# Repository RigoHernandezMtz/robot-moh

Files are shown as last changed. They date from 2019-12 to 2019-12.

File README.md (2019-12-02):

# Robot Moh

## Robot móvil para navegación

Este repositorio contiene los archivos necesarios para poner a funcionar el robot, como:

- Diagrama y PCB en documentos de Eagle
- Archivos de CAD del chasis en formato de Siemens Unigraphics NX 10.5
- Lista de materiales en documento de Excel, y de corte laser del chasis en PDF.
- Codigos, del arduino y de la Raspberry Pi o BeagleBone Black

### Diseño en CAD del robot
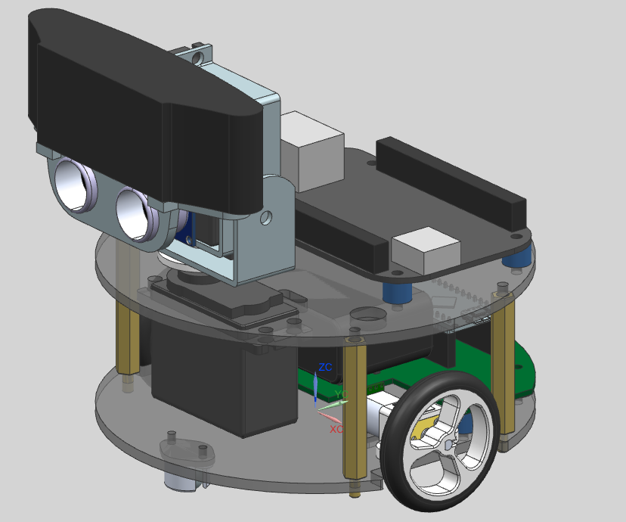
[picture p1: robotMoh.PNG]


---

Diseñado por: **Ing. Gerardo Ramos Vasquez**

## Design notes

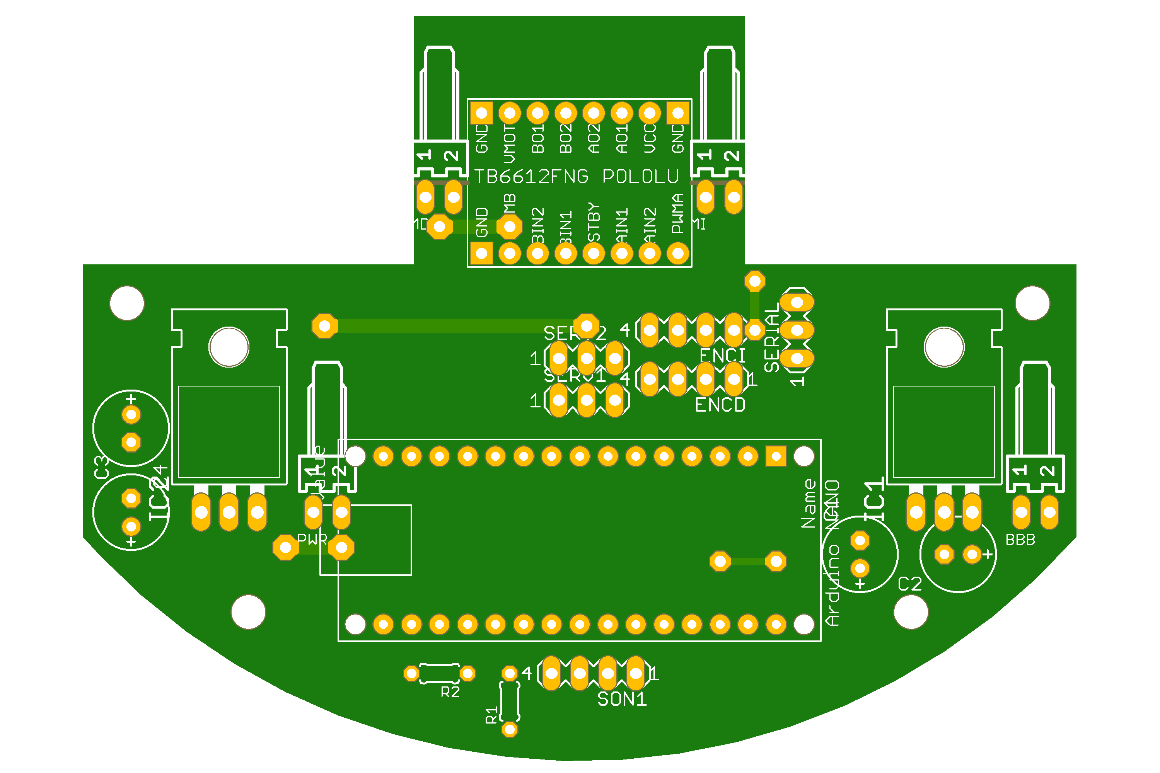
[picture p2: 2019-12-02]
electronica/PCBArduino.png

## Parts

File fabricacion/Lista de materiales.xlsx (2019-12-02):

N | Cant | Descripción | Costo U | Costo T | N parte | Marca | Referencia
 |  | Electronica
1 | 1 | Encoder Magnético para micromotores con eje extendido ( Par) 12 CPR | $160.00 | $160.00 | 2598 | Pololu | http://sandorobotics.com/
3 | 1 | Llantas 40x7mm Par-blancas | $130.00 | $130.00 | 1454 | Pololu | http://sandorobotics.com/
4 | 1 | Rueda loca de metal 3/8 | $35.00 | $35.00 | 951 | Pololu | http://sandorobotics.com/
5 | 1 | Bracket para micromotor par-negro | $80.00 | $80.00 | 989 | Pololu | http://sandorobotics.com/
6 | 2 | Micromotor con reductor metalico HP y eje extendido 100:1 | $290.00 | $580.00 | 2214 | Pololu | http://sandorobotics.com/
7 | 1 | Puente H de 2 canales @1.2A/canal | $90.00 | $90.00 | 713 | Pololu | http://sandorobotics.com/
8 | 2 | Servomotor Hitec HS-422 | $250.00 | $500.00 | HS-422 | Hitec | http://sandorobotics.com/index.php?route=product/product&path=76_88_90&product_id=226
9 | 1 | Webcam Logitech c920 HD-PRO | $1399.00 | $1399.00 | 1000179505 | logitech | http://www.bestbuy.com.mx/productos/computadoras/accesorios-para-computadoras/logitech-hd-pro-webcam-c920.html
10 | 1 | BeagleBone Black rev-C | $1350.00 | $1350.00 | DEV-12857 | beagleboard | http://sandorobotics.com/index.php?route=product/product&product_id=655&search=beaglebone
11 | 1 | Sensor ultrasónico HC-SR04 | $80.00 | $80.00 | HC-SR04 | Itead Studio | http://sandorobotics.com/index.php?route=product/product&path=60_63&product_id=574
12 | 1 | Antena WiFi |  | $0.00
13 | 1 | HUB usb |  | $0.00
 | 1 | Tarjeta PCB electrónica | $50.00 | $50.00 |  |  | Nacho
 | 1 | Arduino Nano | $450.00 | $450.00 | A000005 | Arduino | http://sandorobotics.com/index.php?route=product/product&product_id=171&search=arduino+nano
 | 1 | Regulador 5V @1.5A |  | $0.00
 | 1 | regulador 6V @1A |  | $0.00
 | 1 | Bateria 7.4V @1000mAh | $180.00 | $180.00 | HD1000HP-2S | Power HD | http://sandorobotics.com/index.php?route=product/product&path=97_99&product_id=408
 |  |  |  | $0.00
 |  | Raspberry Pi 2 |  | $0.00 |  |  | http://www.330ohms.com/Raspberry-Pi-2--Modelo-B-1-Gb_p_537.html
 |  |  |  | $0.00
 |  |  |  | $0.00
 |  |  |  | $0.00
 |  |  |  | $0.00
14 |  |  |  | $0.00
 |  | Mecanica |  | $0.00
1 | 1 | Corte chasis en acrilico + material | $95.00 | $95.00 |  |  | http://www.330ohms.com/
16 | 1 | Corte de soporte sonar en acrilico | $30.00 | $30.00 |  |  | http://www.330ohms.com/
17 | 4 | Tornillo M4x10 | $1.00 | $4.00
18 | 4 | Tuerca M4 | $1.00 | $4.00
19 | 8 | Tornillo M3x10 | $1.00 | $8.00
20 | 4 | Tornillo M3x15 | $1.50 | $6.00
21 | 16 | Tuerca M3 | $1.00 | $16.00
22 | 4 | Espaciador hex 40mm x 1/4 x rosca M3 | $5.00 | $20.00
 |  |  |  | $0.00
 |  |  |  | $0.00
 |  |  |  | $0.00
 |  |  |  | $0.00
 |  |  |  | $5267.00

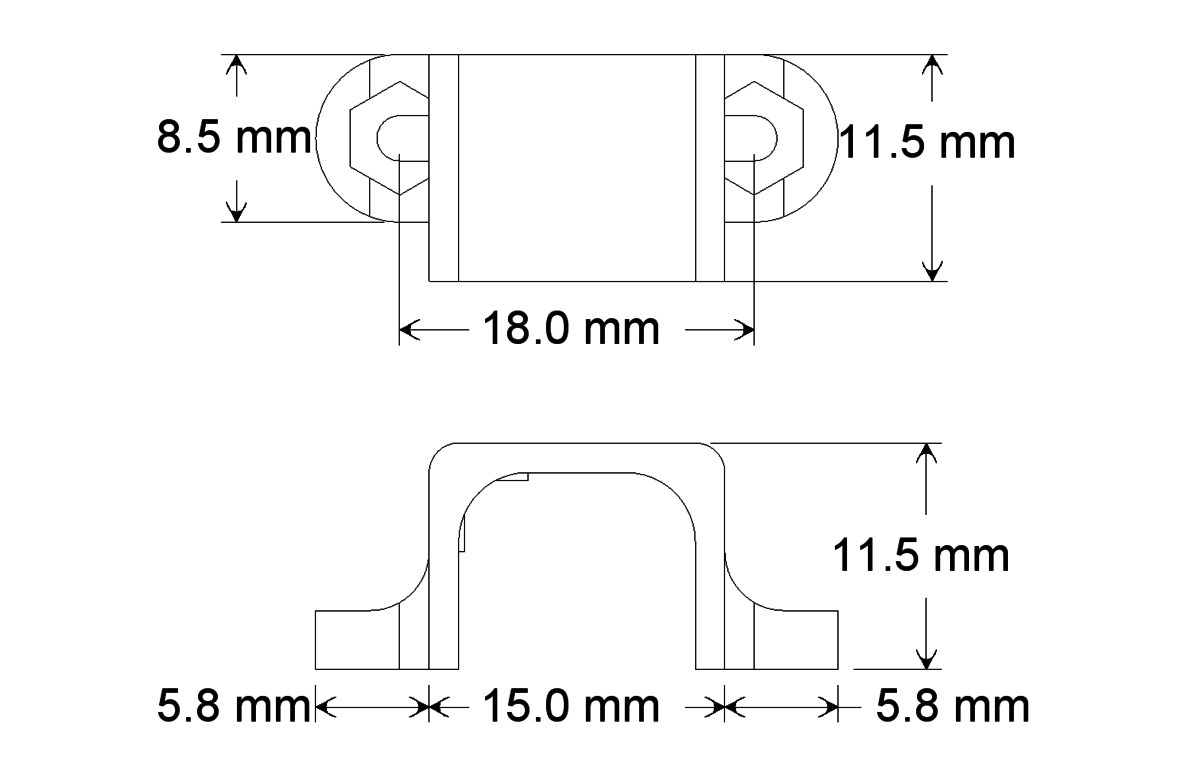
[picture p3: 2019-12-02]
componentes/bracket.jpg

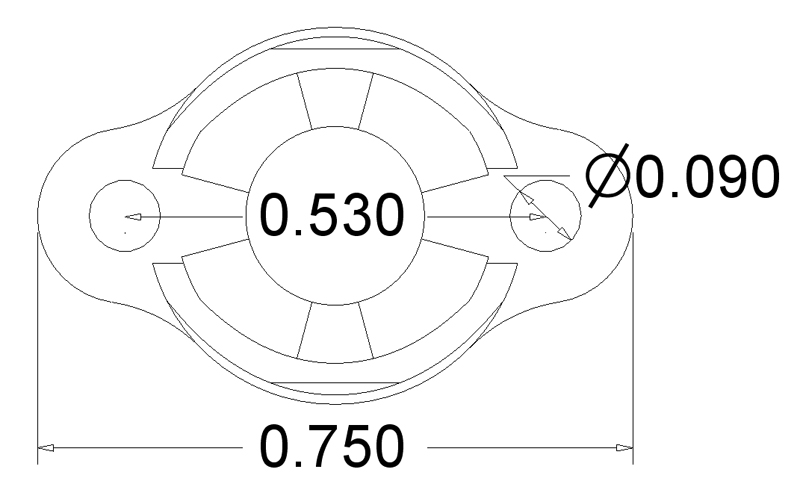
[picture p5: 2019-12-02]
componentes/BallCaster3-8v1.jpg

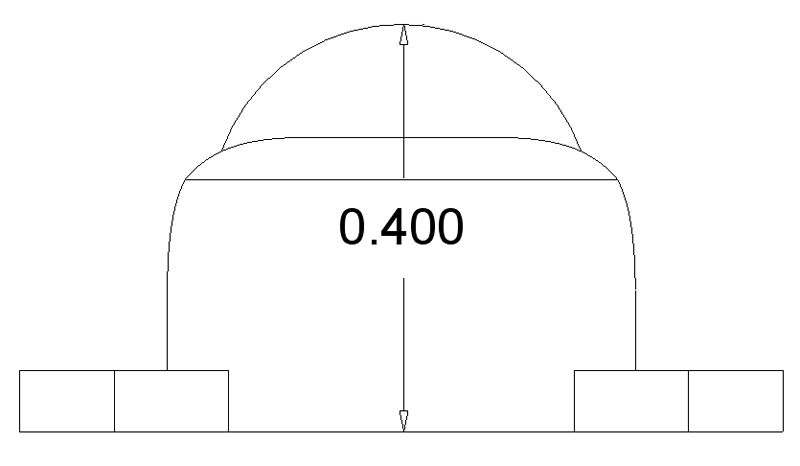
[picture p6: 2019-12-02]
componentes/BallCaster3-8v2.jpg

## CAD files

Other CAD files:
mecanica/Arduino Mini ASSY.prt
mecanica/ArduinoMini.prt
mecanica/BallCaster3-8Metal.prt
mecanica/BaterialLiPo_7-4_1000.prt
mecanica/BeagleBoneBlack.prt
mecanica/CopleServo.prt
mecanica/Encoder.prt
mecanica/HC-SR04.prt
mecanica/HC-SR04_RobDEC.prt
mecanica/Logitech_c920.prt
mecanica/Motor_Brack_Enc.prt
mecanica/PCB_Arduino.prt
mecanica/PuenteH.prt
mecanica/Robot.prt
mecanica/Rueda40x7.prt
mecanica/SepCast.prt
mecanica/SepChasis.prt
mecanica/ServoSdt.prt
mecanica/SopServo1.prt
mecanica/SopServo2.prt
mecanica/SopSon1.prt
mecanica/SopSon2.prt
mecanica/Stellaris.prt
mecanica/StellarisLaunch.prt
mecanica/StellarisShield.prt
mecanica/UltraSonic.prt
mecanica/UserLibrary-MicroUSB.prt
mecanica/chasis_inf.prt
mecanica/chasis_sup1.prt
mecanica/espaciador6mm.prt
mecanica/iman.prt
mecanica/microMotor-Bracket.prt
mecanica/part2.prt
mecanica/pin header.prt
mecanica/pin_header_aw254-dg-g32d_6Pin.prt
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

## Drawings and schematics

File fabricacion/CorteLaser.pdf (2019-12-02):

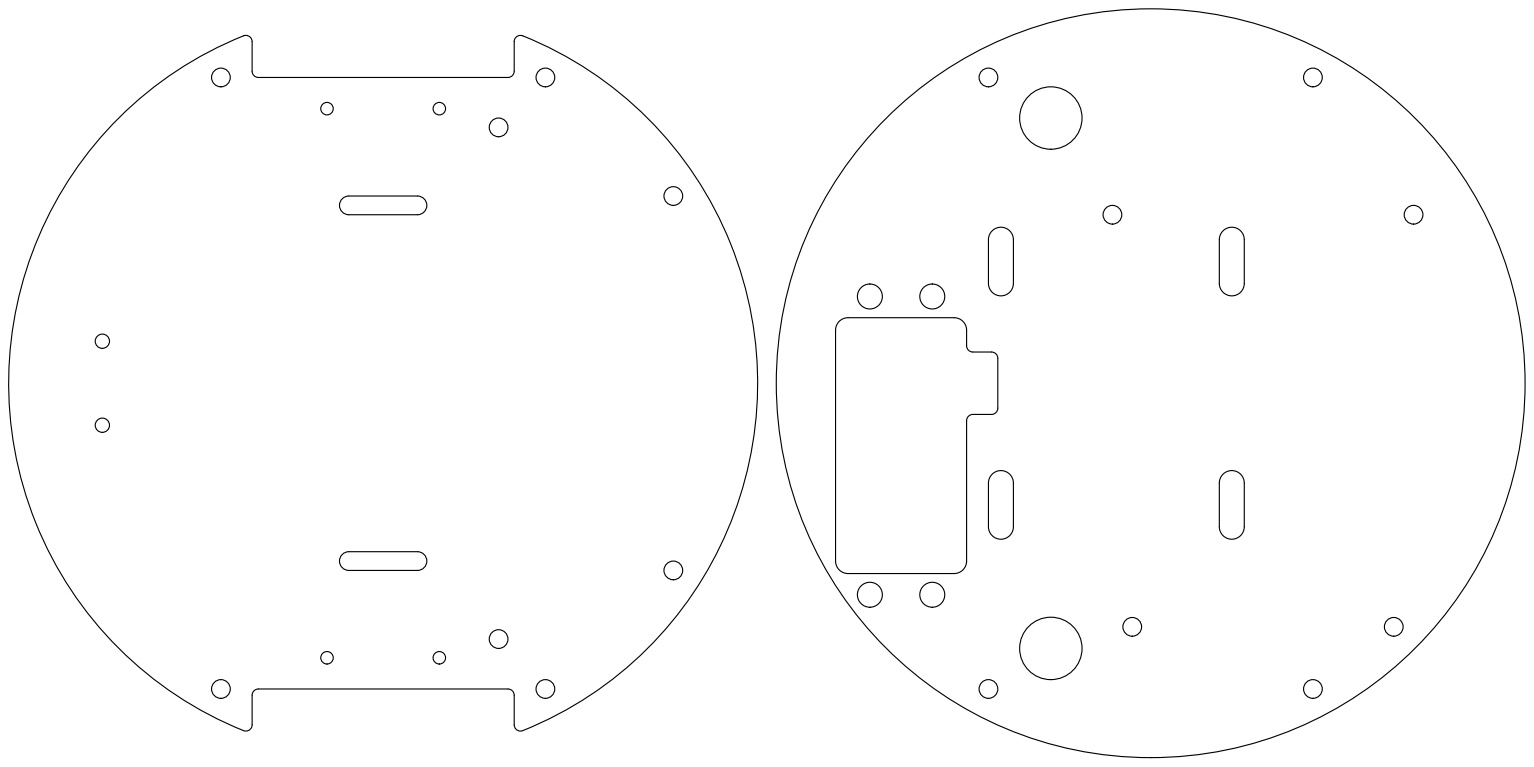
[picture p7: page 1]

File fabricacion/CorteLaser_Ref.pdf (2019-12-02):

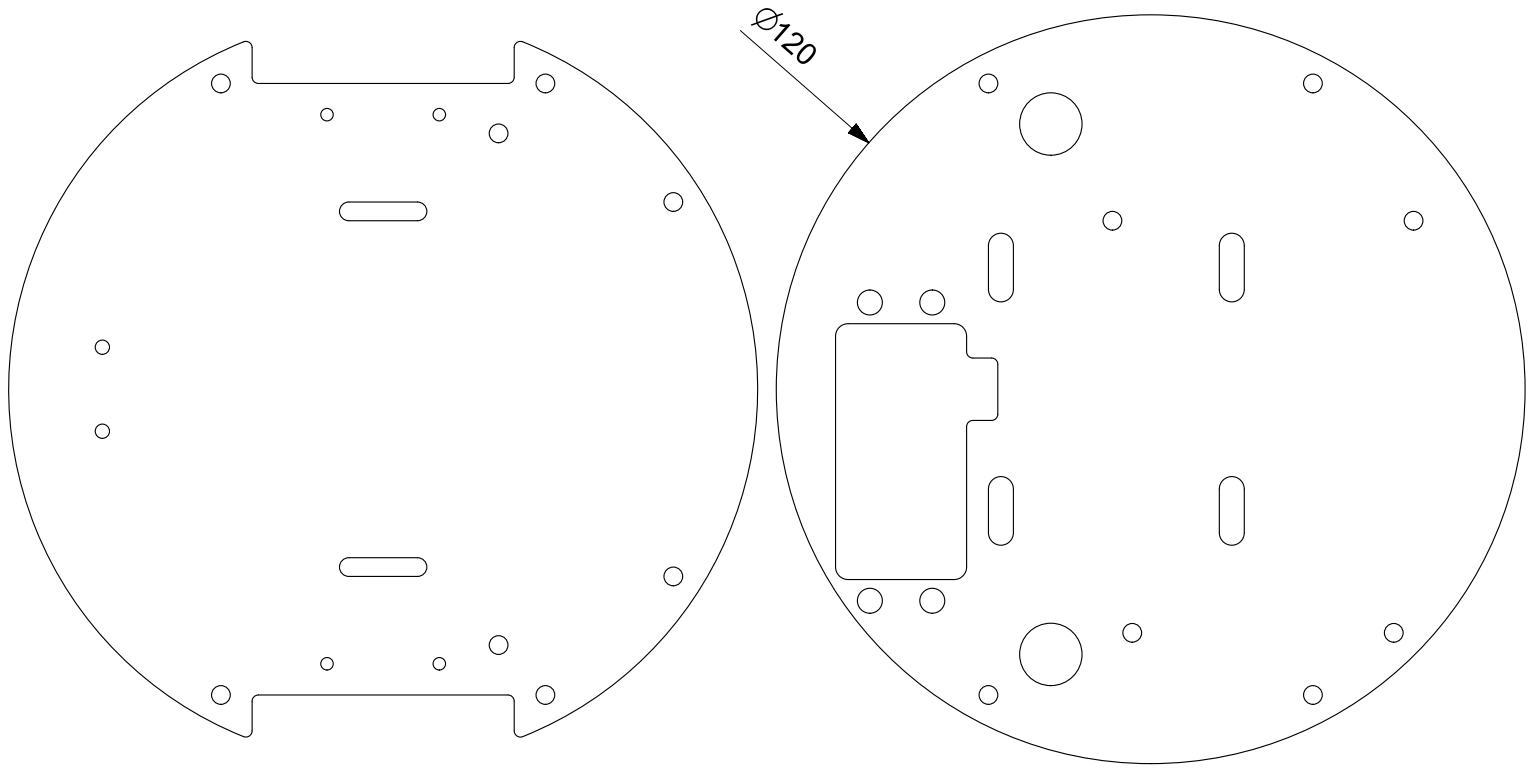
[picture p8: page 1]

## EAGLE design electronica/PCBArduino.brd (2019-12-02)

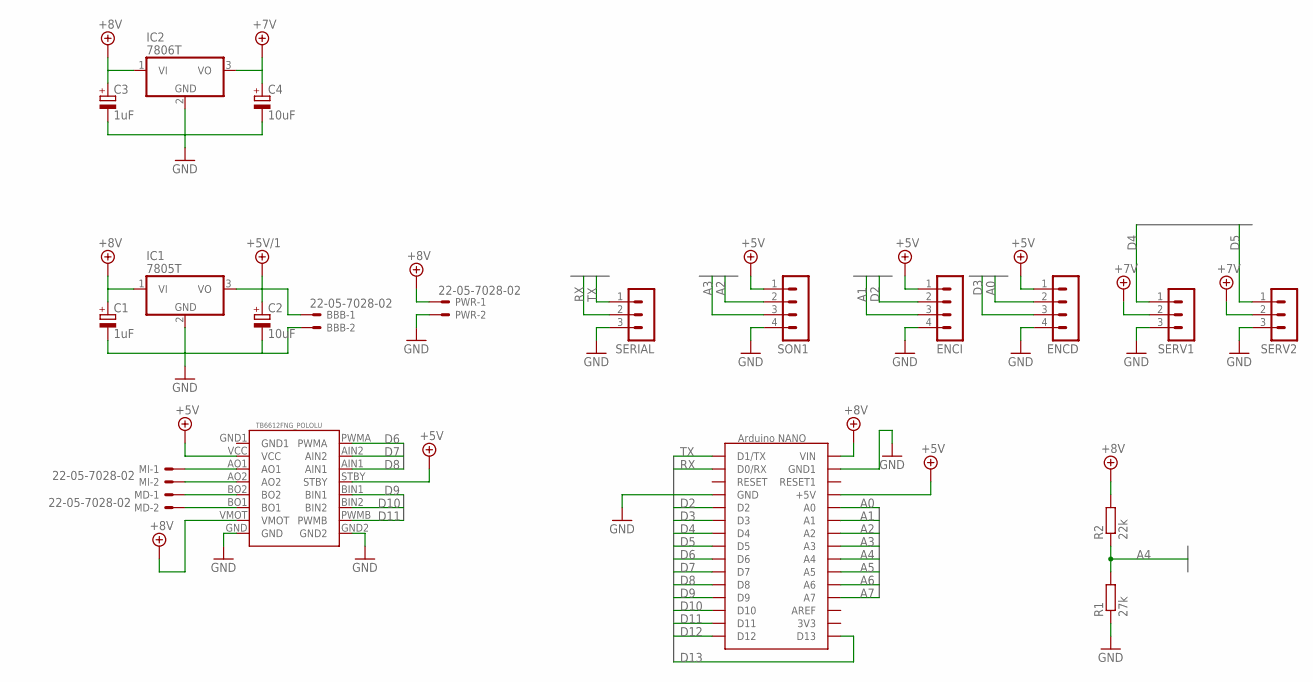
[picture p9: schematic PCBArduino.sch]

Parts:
BBB: 22-05-7028-02; 7395-02
C1, C3: 1uF; E2,5-7
C2, C4: 10uF; E2,5-7
ENCD: MA04-1
ENCI: MA04-1
IC1: 7805T; TO220H
IC2: 7806T; TO220H
MD: 22-05-7028-02; 7395-02
MI: 22-05-7028-02; 7395-02
PWR: 22-05-7028-02; 7395-02
R1: 27k; 0204/5
R2: 22k; 0204/5
SERIAL: MA03-1
SERV1, SERV2: MA03-1
SON1: MA04-1
U$1: ARDUINONANO; PDIP-32
U$2: TB6612FNG_POLOLU

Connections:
+5V: ENCD.1, ENCI.1, SON1.1, U$1.+5V, U$2.STBY, U$2.VCC
+5V/1: BBB.1, C2.+, IC1.3 (VO)
+7V: C4.+, IC2.3 (VO), SERV1.2, SERV2.2
+8V: C1.+, C3.+, IC1.1 (VI), IC2.1 (VI), PWR.1, R2.2, U$1.VIN, U$2.VMOT
A0: ENCD.2, U$1.A0
A1: ENCI.3, U$1.A1
A2: SON1.2, U$1.A2
A3: SON1.3, U$1.A3
A4: R1.2, R2.1, U$1.A4
A5: U$1.A5
A6: U$1.A6
A7: U$1.A7
D2: ENCI.2, U$1.D2
D3: ENCD.3, U$1.D3
D4: SERV1.1, U$1.D4
D5: SERV2.1, U$1.D5
D6: U$1.D6, U$2.PWMA
D7: U$1.D7, U$2.AIN2
D8: U$1.D8, U$2.AIN1
D9: U$1.D9, U$2.BIN1
D10: U$1.D10, U$2.BIN2
D11: U$1.D11, U$2.PWMB
D12: U$1.D12
D13: U$1.D13
GND: BBB.2, C1.-, C2.-, C3.-, C4.-, ENCD.4, ENCI.4, IC1.2 (GND), IC2.2 (GND), PWR.2, R1.1, SERIAL.3, SERV1.3, SERV2.3, SON1.4, U$1.GND, U$1.GND1, U$2.GND, U$2.GND2
unnamed: MI.1, U$2.AO1
unnamed: MI.2, U$2.AO2
unnamed: MD.1, U$2.BO2
unnamed: MD.2, U$2.BO1
RX: SERIAL.2, U$1.D0/RX
TX: SERIAL.1, U$1.D1/TX

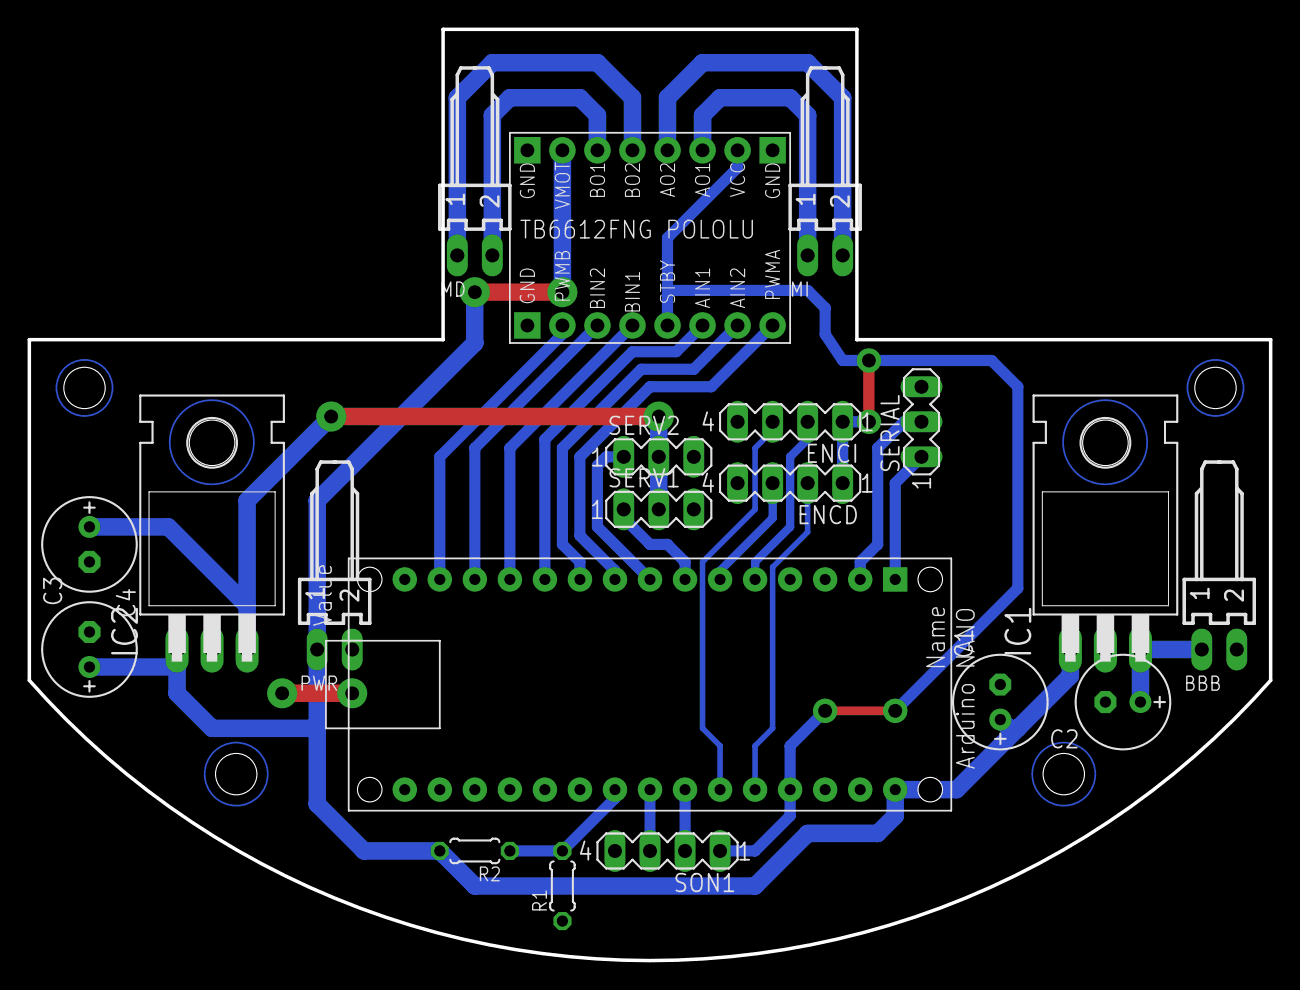
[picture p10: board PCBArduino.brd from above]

Board: 2 copper layers, 90.0 x 67.5 mm, 20 parts (0 on the bottom side), 26 nets.

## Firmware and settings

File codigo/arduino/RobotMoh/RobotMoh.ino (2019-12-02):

#include <Servo.h>
#define ECHO_PIN A4
#define TRIGER_PIN A5
#define S1_PIN  4
#define S2_PIN  5
#define ENCD_A    0  //Digital PIN 2
#define ENCD_B    A0  //Digital PIN 22
#define ENCI_A    1  //Digital PIN 3
#define ENCI_B    A1  //Digital PIN 23
#define VOLT_PIN  A3
#define MOTD_A  7
#define MOTD_B  8
#define MOTD_P  6

#define MOTI_A  9
#define MOTI_B  10
#define MOTI_P  11

#define LED 13

int time=0;

Servo s1;
Servo s2;
long encD=0,encI=0;
long t0=millis();
long t0Rem=millis();
long vDer=0,vIzq=0;
long s[2]={90,90};
float volt;
void setup(){
  pinMode(ECHO_PIN,INPUT);
  pinMode(TRIGER_PIN,OUTPUT);
  pinMode(LED,OUTPUT);
  Serial.begin(115200);
  s1.attach(S1_PIN);
  s2.attach(S2_PIN);
  s1.write(90);
  s2.write(80);
  attachInterrupt(ENCD_A,inte0,RISING);
  attachInterrupt(ENCI_A,inte1,RISING);
  pinMode(MOTD_A,OUTPUT);
  pinMode(MOTD_B,OUTPUT);
  pinMode(MOTI_A,OUTPUT);
  pinMode(MOTI_B,OUTPUT);
}

void loop(){
  s1.write(s[0]);
  s2.write(s[1]);
  
  if((millis()-t0)>200){
    time=leer_sonar()/10;
    t0=millis();
  }
  if((millis()-t0Rem)>500)
    motores(0,0);
    

  volt=analogRead(VOLT_PIN);
  volt=volt*9.05/1024;
  remoto();
}

long leer_sonar(){
   long tempo=0;
   digitalWrite(TRIGER_PIN,HIGH);
   delayMicroseconds(11);
   digitalWrite(TRIGER_PIN,LOW);
   int err=0;   
   while(!digitalRead(ECHO_PIN) && err<4000){
     err+=1; 
   }
   if(err<4000){
      while(digitalRead(ECHO_PIN) && tempo<1000)
         tempo=tempo+1;   
   }
   else
      tempo=9999;
   return tempo;
}




void inte0(){
  if(digitalRead(ENCD_B)){
    encD=encD-1;
  }
  else{
    encD=encD+1;
  }
}
void inte1(){
  if(!digitalRead(ENCI_B)){
    encI=encI+1;
  }
  else{
    encI=encI-1;
  }
}

void motores(float vi, float vd){
  if(vi>0){
    digitalWrite(MOTI_A,HIGH);
    digitalWrite(MOTI_B,LOW);
  }
  else{
    digitalWrite(MOTI_A,LOW);
    digitalWrite(MOTI_B,HIGH);
  }
  if(vd>0){
    digitalWrite(MOTD_A,HIGH);
    digitalWrite(MOTD_B,LOW);
  }
  else{
    digitalWrite(MOTD_A,LOW);
    digitalWrite(MOTD_B,HIGH);
  }
  analogWrite(MOTI_P,abs(vi*2.55));
  analogWrite(MOTD_P,abs(vd*2.55));
}

void remoto(){
  char temp;
  char dataIn[13];
  int i=0;
  if(Serial.available()>12){
    temp=Serial.read();
    if(temp=='#'){
      temp=Serial.read();
      if(temp=='O'){
        i=0;
        while(i<11){
          dataIn[i]=Serial.read();
          i+=1;
        }//fin while 11
        char crc=0;
        for(i=0;i<10;i++)
          crc+=dataIn[i];
        if(crc==dataIn[10]){
          //acondicionamiento de variables
          digitalWrite(LED,dataIn[0]);
          
          vIzq=byte(dataIn[1]);
          vIzq-=128;
          if(vIzq<-100)
            vIzq=-100;
          if(vIzq>100)
            vIzq=100;
            
          vDer=byte(dataIn[2]);
          vDer-=128;
          if(vDer<-100)
            vDer=-100;
          if(vDer>100)
            vDer=100;
            
          s[0]=byte(dataIn[3]);
          if(s[0]>180)
            s[0]=180;
          s[1]=byte(dataIn[4]);
          if(s[1]>180)
            s[1]=180;
          
          //fin acodicionamiento
          //envio de datos
          Serial.print("Robot:");
          Serial.print(encD);
          Serial.print(" ");
          Serial.print(encI);
          Serial.print(" ");
          Serial.print(time);
          Serial.print(" ");
          Serial.print(volt);
          Serial.print(" ");
          Serial.println(101);
          //fin de envio de datos
          motores(vIzq,vDer);
          t0Rem=millis();
        }//fin crc
        
      }//fin O

    }//fin #

  }//fin lectura 12
} // fin remoto()

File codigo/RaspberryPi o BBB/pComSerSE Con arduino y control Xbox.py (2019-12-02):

import serial
import time
import threading
import random
import socket

UDP_IPRecv="192.168.0.122"
UDP_PORTRecv=5005

UDP_IP="192.168.0.100"
UDP_PORT=5005

#sock=socket.socket(socket.AF_INET,socket.SOCK_DGRAM)
#sock.bind((UDP_IP,UDP_PORT))

class Remote(threading.Thread):
	def __init__(self):
		print "Control remoto creado"
		threading.Thread.__init__(self)
		self.udpIP="127.0.0.1"
		self.udpPort=15555
		self.udpIPRecv="127.0.0.1"
		self.udpPortRecv=15666
		self.instruction="None"
		self.messFromJoy="None"
		self.thereMess=False
		self.isRunning=True
	def SetSocketToSend(self,ip,port):
		self.udpIP=ip
		self.udpPort=port
		self.sock=socket.socket(socket.AF_INET,socket.SOCK_DGRAM)
	def SetSocketToRecv(self,ip,port):
		self.udpIPRecv=ip
		self.udpPortRecv=port
		self.sockRecv=socket.socket(socket.AF_INET,socket.SOCK_DGRAM)
	def SendInfo(self,cad):
		stringOut="robot:"+cad
		self.sock.sendto(stringOut,(self.udpIP,self.udpPort))
	
	def run(self):
		self.sockRecv.bind((self.udpIPRecv,self.udpPortRecv))
		print "leyendo datos del remoto"
		while self.isRunning:
			data,addr=self.sockRecv.recvfrom(1024)
			temp=data.split(":")
			if len(temp)==4:
				if temp[0]=="Robot" and temp[1]=="robot123":
					if temp[2]=="EndProgram":
						self.isRunning=False
						self.instruction="EndProgram"
					if temp[2]=="JoyStick":
						self.messFromJoy=temp[3]
						self.thereMess=True


class RobotBase(threading.Thread):
	def __init__(self,real):
		threading.Thread.__init__(self)
		print "Robot iniciado"
		self.real=real
		self.dataOut=[0,128,128,90,90,0,0,0,0,0]
		self.dataIn=[0,0,0,0,0,0,0,0,0,0]
		self.runBase=True
		self.mot=[0,0]
		self.serv=[90,90]
		self.encD= 0.0
		self.encI= 0.0
		self.sonar=0.0
		self.volt= 0.0

	def SetSerial(self,port,baud):
		if self.real:
			self.ser=serial.Serial(port,baud,timeout=0.5)
	def ComBase(self):
		if self.real:
			self.dataOut[1]=self.mot[0]+128
			self.dataOut[2]=self.mot[1]+128
			if self.serv[0]>105:
				 self.dataOut[3]=105
			elif self.serv[0]<30:
                                 self.dataOut[3]=30
			else:
				self.dataOut[3]=self.serv[0]
			self.dataOut[4]=self.serv[1]
			if self.dataOut[0]==1:
				self.dataOut[0]=0
			else:
				self.dataOut[0]=1
			out="#O"
			crc=0
			for e in self.dataOut:
				out+=chr(e)
				crc+=e
			while crc>255:
				crc-=256
			out+=chr(crc)
			self.ser.write(out)
			self.ser.flush()#vaciar buffer del puerto serie
			time.sleep(0.01)
			buff=self.ser.readline()
			cad=buff.split(":")
			if cad[0]=="Robot" and len(cad)==2:
				c=cad[1].split(" ")
				if len(c)==5:
					self.encD= float(c[0])
					self.encI= float(c[1])
					self.sonar=float(c[2])
					self.volt= float(c[3])

	def run(self):
		while self.runBase:
			self.ComBase()
			time.sleep(0.01)
	
	def Remote(self,mess,th):
		if th==True:
			cad=mess.split("_")
			if len(cad)==2:
				if cad[0]=="motores":
					m=cad[1].split(" ")
					if len(m)==2:
						self.mot[0]=int(m[0])
						self.mot[1]=int(m[1])
				if cad[0]=="pan":
					self.serv[1]=int(cad[1])
				if cad[0]=="tilt":
					self.serv[0]=int(cad[1])



base=RobotBase(True)
base.SetSerial('/dev/ttyO4',115200)
base.start()

remoto=Remote()
remoto.SetSocketToSend(UDP_IP,UDP_PORT)#IP Remoto
remoto.SetSocketToRecv(UDP_IPRecv,UDP_PORTRecv)#IP Robot
remoto.start()

j=0
i=0
while base.runBase:
	base.Remote(remoto.messFromJoy,remoto.thereMess)
	time.sleep(0.1)
	print "c:",i,"Salida:",base.dataOut,"Entrada:",base.dataIn
	infoS=str(base.encI)+" "+str(base.encD)+" "
	infoS+=str(base.sonar)+" "+str(base.volt)
	if i%10==0:
		remoto.SendInfo(infoS)
	base.runBase=remoto.isRunning
	i+=1
